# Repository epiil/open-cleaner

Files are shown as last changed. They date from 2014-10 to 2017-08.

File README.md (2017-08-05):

# opencleaner: open-source videotape cleaning

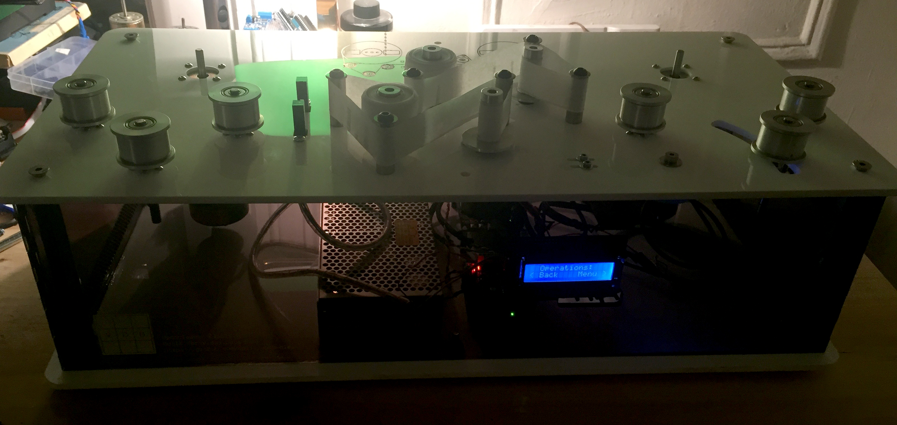
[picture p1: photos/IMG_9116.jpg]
Opencleaner


## Introduction

This repo contains instructions for assembling, testing, and operating an open-reel 1/2" magnetic videotape cleaner. When used in conjunction with other remediation treatments like incubation, tape cleaning assists in minimizing the effects of tape degradation such as binder hydrolysis ("sticky shed syndrome") during the playback/reformatting process.  

Controlled by an Arduino Uno microcontroller and integrated motor shield, the machine consists of a dual-motor spindle system that moves tape through two Pellon cleaning stations. Tape speed and tension are monitored through feedback from optical encoders attached to each motor's shaft. Each Pellon cleaning station incrementally advances fabric past several contact points.  

In-progress videos:

[02/15/2017 - 24VDC Motor Test](https://vimeo.com/204296759)

[02/23/2017 - PID Control Test](https://vimeo.com/205490774)

##Repository Contents:

- /hardware - contains .dwg, .pdf, .stp and .stl files for enclosure and spindle fabrication.

- /software - contains .ino Arduino sketches (http://www.arduino.cc/).

- /schematics - contains .sch and .pdf schematic files for individual components.

- /photos - photo gallery

## Acknowledgements

This project could not have been possible without the generous contributions from the following people and organizations:

Tim Woolaver

Mike Maxwell

Maurice Schechter

Video Data Bank - Tom Colley, Kristin McDonough

Smithsonian NMAAHC - Walter Forsberg

Signal Culture - Deborah Bernagozzi, Jason Bernagozzi, Hank Rudolph

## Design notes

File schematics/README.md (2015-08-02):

- /ComponentSchematics - contains fact sheets for inividual components

- /png - contains .png image of associated schematic

- /sch - contains .sch schematic files done in Eagle (http://www.cadsoftusa.com/)

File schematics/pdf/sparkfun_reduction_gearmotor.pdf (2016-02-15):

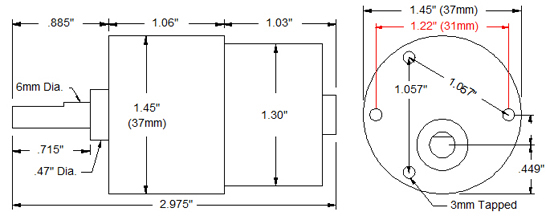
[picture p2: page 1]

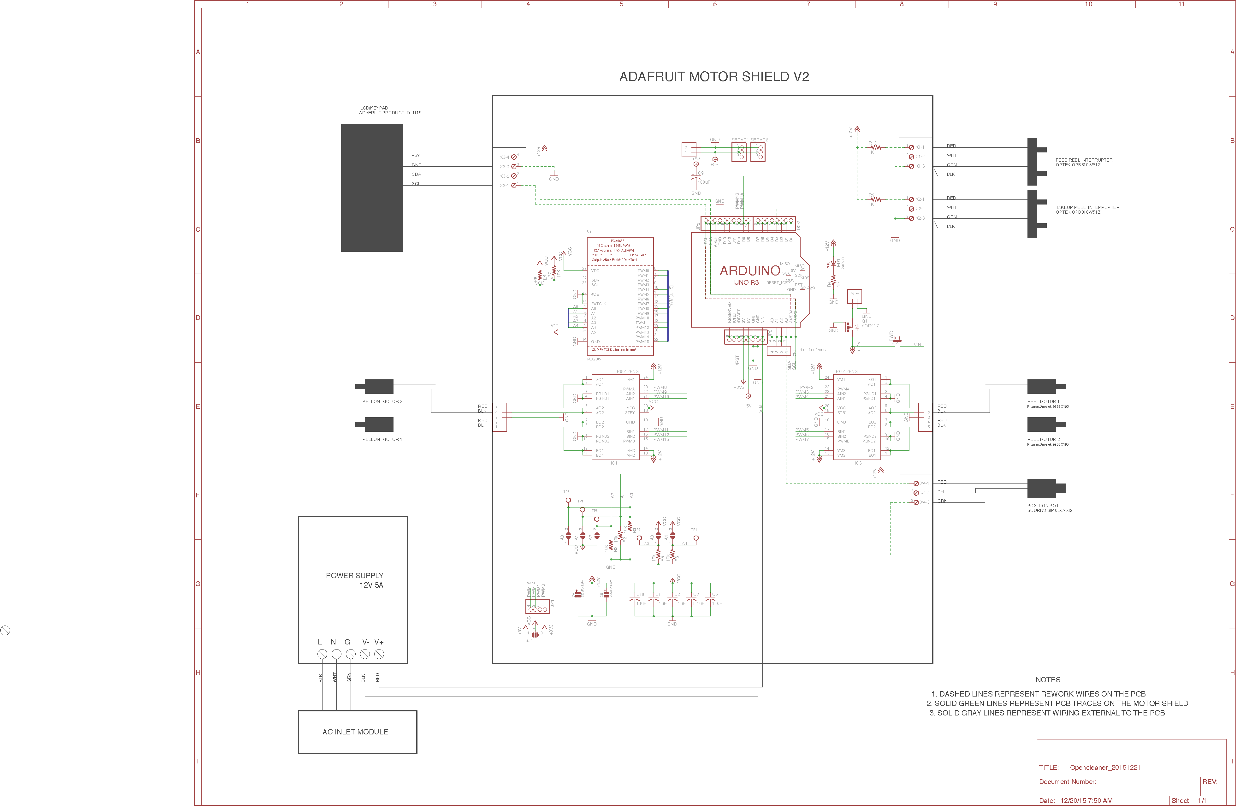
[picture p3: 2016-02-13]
schematics/png/Opencleaner_20151221.png

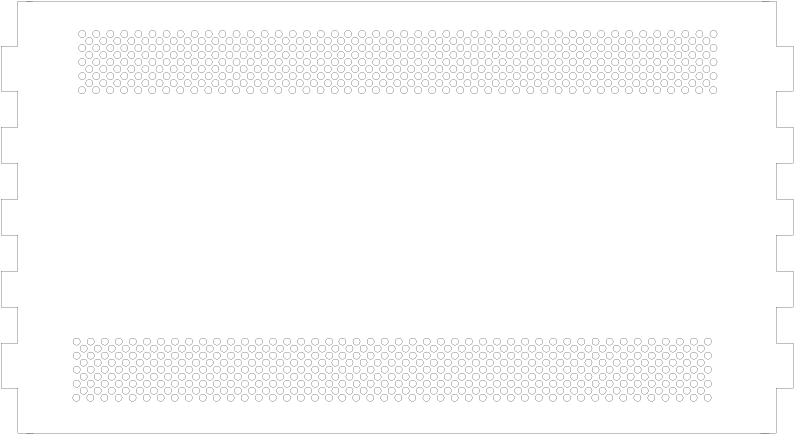
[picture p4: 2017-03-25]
hardware/enclosure/png/20170324 - Opencleaner - Side Panels.png

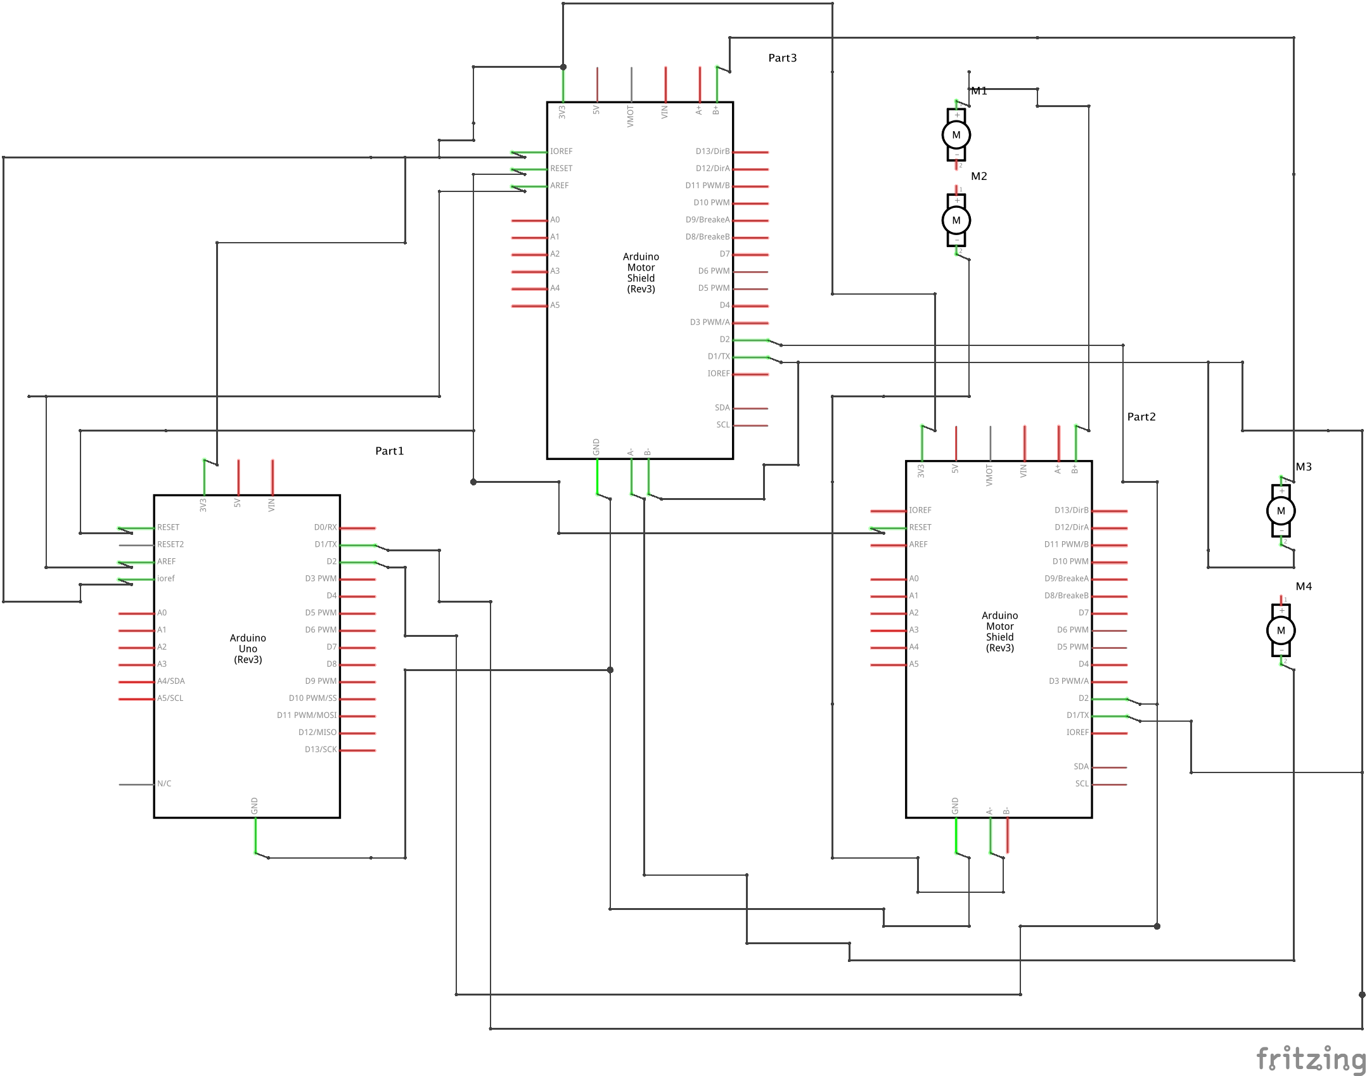
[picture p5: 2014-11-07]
hardware/3_circuit_schematics/png/20141106_tape_cleaner_schem.png

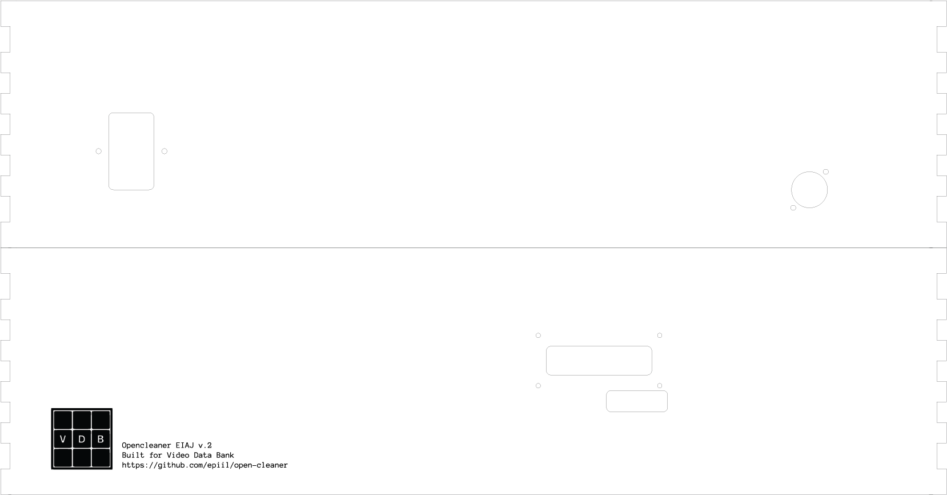
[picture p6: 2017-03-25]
hardware/enclosure/png/20160324 - OpenCleaner - FrontBack Panel.png

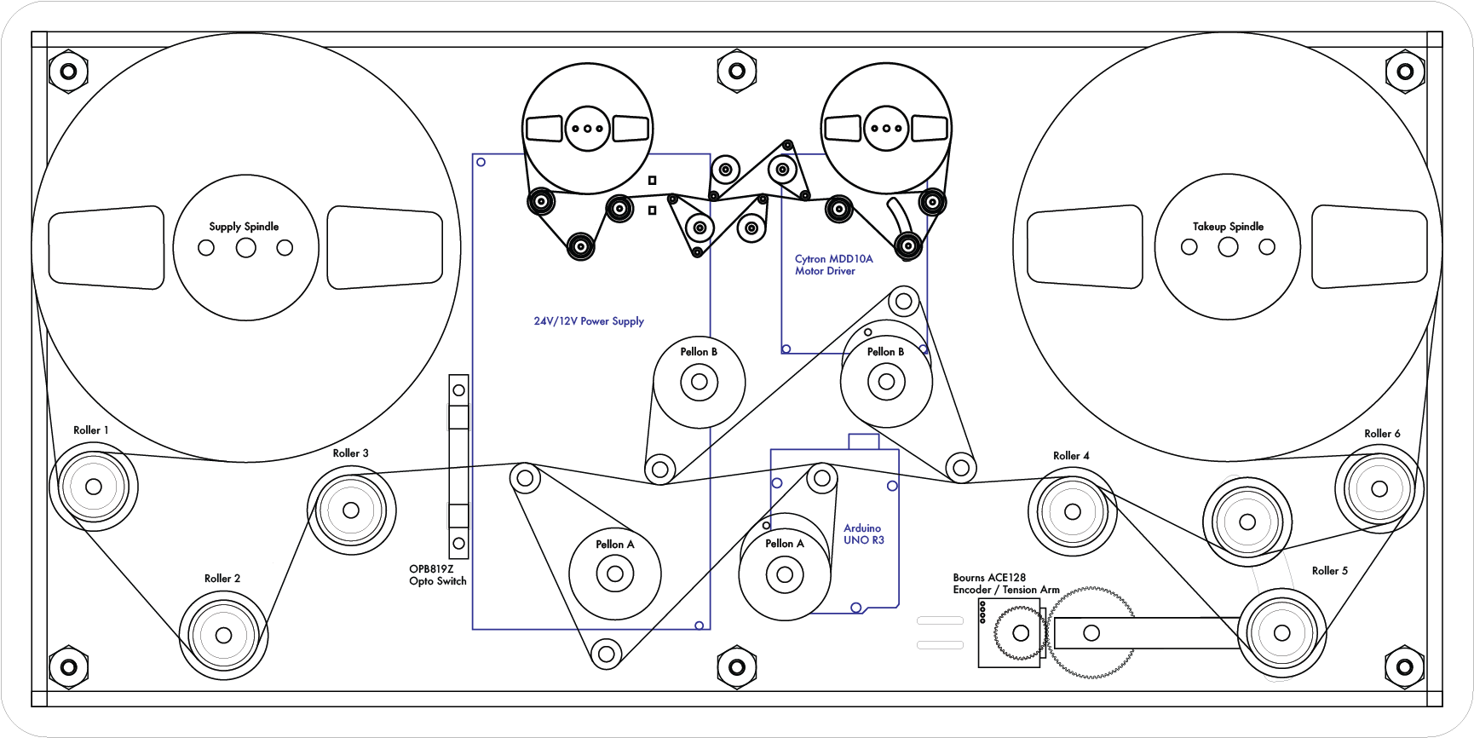
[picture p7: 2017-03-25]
hardware/enclosure/png/20170323 - Opencleaner - Top Panel.png

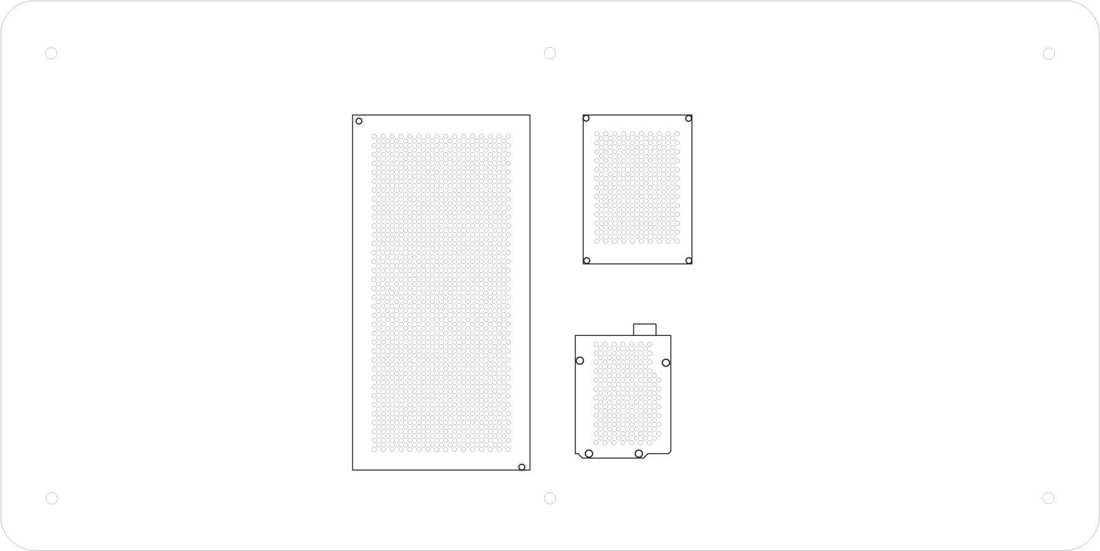
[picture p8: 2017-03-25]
hardware/enclosure/png/20170323 - Opencleaner - Bottom Panel.png

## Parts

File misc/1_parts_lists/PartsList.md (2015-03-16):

##Parts List (Updated 11/18/2014)

###Enclosure

- (1) 350DT 16"W x 16"D aluminum desktop enclosure, natural finish
- Chassis: Extruded Aluminum (6063 T6)
- Top/Bottom/Endplates: Aluminum (5052 H32)

###Main circuit boards / microcontrollers

- (1) Arduino Uno Rev3 Microcontroller board
- (1) Arduino Motor Shield Rev3 (http://arduino.cc/en/Main/ArduinoMotorShieldR3)
- (2) Sparkfun Photo Interrupter Breakout Board - GP1A57HRJ00F

###Motors

- (2) Seiko Continuous Sweep Hi-Torque Quartz Clock Motors
- (2) Brushed DC Motors 

###Cleaning fabric

- (2) Amber Professional Pellon Non-Woven Rolls

###Circuit components

- (2) TIP120 Power Darlington Transistors
- (2) NPN Bipolar Transistors (PN2222) 
- (2) 1N4001 Diodes
- (2) 330 Ohm resistors
- (2) Photo Interrupters - GP1A57HRJ00F
- (1) DPDT switch
- (1) SPDT switch
- (2) LM317TG voltage regulators
- (2) Heatsinks TO-220
- (2) 0.1uF capacitors
- (2) Sharp GP2Y0A21YK0F IR Range Sensors
- (2) SIRC-01 Sharp GP2 IR Sensor Cables

###Misc.

- (1) IEC 320 C14 Male Plug 3 Pins PCB Panel Power Inlet Socket Connector

-----

###(Updated 11/18/2014)

- $ 24.99 (1) Arduino Uno Rev3 
- $ 24.99 (1) Arduino Motor Shield Rev3
- $ 29.90 (2) Seiko Continuous Sweep Hi-Torque Quartz Clock Motors
- $ 33.94 (2) Amber Professional Pellon Non-Woven Rolls
- $ 40.00 (2) Brushed DC Motors
- $  2.50 (1) TIP120 Power Darlington Transistors - 3 pack[ID:976] via Adafruit
- $  1.95 (1) NPN Bipolar Transistors (PN2222) - 10 pack[ID:756] via Adafruit
- $  3.00 (2) 1N4001 Diode - 10 pack[ID:755] via Adafruit
- $  3.00 (2) Sparkfun Photo Interrupter Breakout Board - GP1A57HRJ00F
- $   .50 (2) 330 Ohm resistors
- $  3.90 (2) Photo Interrupters - GP1A57HRJ00F
- $  1.95 (1) DPDT switch
- $  1.95 (1) SPDT switch
- $  7.80 (2) LM317TG voltage regulators
- $  3.80 (2) Heatsinks TO-220
- $   .50 (2) 0.1uF capacitors
- $ 19.90 (2) Sharp GP2Y0A21YK0F IR Range Sensors
- $  3.90 (2) SIRC-01 Sharp GP2 IR Sensor Cables
- $142.95 (1) 350DT 16"W x 16"D aluminum desktop enclosure, natural finish

- $351.42 Total

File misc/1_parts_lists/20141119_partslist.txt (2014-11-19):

Parts List (Updated 11/18/2014)

1. Main circuit boards / microcontrollers

(1) Arduino Uno Rev3 Microcontroller board
(1) Arduino Motor Shield Rev3 (http://arduino.cc/en/Main/ArduinoMotorShieldR3)
(2) Sparkfun Photo Interrupter Breakout Board - GP1A57HRJ00F

2. Motors

(2) Seiko Continuous Sweep Hi-Torque Quartz Clock Motors
(2) Brushed DC Motors 

3. Cleaning fabric

(2) Amber Professional Pellon Non-Woven Rolls

4. Circuit components

(2) TIP120 Power Darlington Transistors
(2) NPN Bipolar Transistors (PN2222) 
(2) 1N4001 Diodes
(2) 330 Ohm resistors
(2) Photo Interrupters - GP1A57HRJ00F
(1) DPDT switch
(1) SPDT switch
(2) LM317TG voltage regulators
(2) Heatsinks TO-220
(2) 0.1uF capacitors

-----

Price List (Updated 11/18/2014)

$24.99 (1) Arduino Uno Rev3 
$24.99 (1) Arduino Motor Shield Rev3
$29.90 (2) Seiko Continuous Sweep Hi-Torque Quartz Clock Motors
$33.94 (2) Amber Professional Pellon Non-Woven Rolls
$40.00 (2) Brushed DC Motors
$ 2.50 (1) TIP120 Power Darlington Transistors - 3 pack[ID:976] via Adafruit
$ 1.95 (1) NPN Bipolar Transistors (PN2222) - 10 pack[ID:756] via Adafruit
$ 3.00 (2) 1N4001 Diode - 10 pack[ID:755] via Adafruit
$ 3.00 (2) Sparkfun Photo Interrupter Breakout Board - GP1A57HRJ00F
$  .50 (2) 330 Ohm resistors
$ 3.90 (2) Photo Interrupters - GP1A57HRJ00F
$ 1.95 (1) DPDT switch
$ 1.95 (1) SPDT switch
$ 7.80 (2) LM317TG voltage regulators
$ 3.80 (2) Heatsinks TO-220
$  .50 (2) 0.1uF capacitors

$184.67 Total

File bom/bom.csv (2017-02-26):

Component | Quantity | Item | Vendor | Price Per Item | Line Total | Item link
Rollers | 6 | Precision Rollers | tnsmachineworks.com | $55.00 | $330.00 | N/A
Cleaning Station | 4 | Pellon Mounts | tnsmachineworks.com | $40.00 | $160.00 | N/A
Reel Spindles | 2 | Spindle Mounts | tnsmachineworks.com | $40.00 | $80.00 | N/A
Electronics | 1 | Arduino Uno Rev3 Microcontroller board | adafruit.com | $24.95 | $24.95 | https://www.adafruit.com/products/50
Electronics | 1 | Adafruit Motor/Stepper/Servo Shield for Arduino v2 Kit (v2.3) | adafruit.com | $19.95 | $19.95 | https://www.adafruit.com/products/1438
Electronics | 1 | Adafruit Blue&White 16x2 LCD+Keypad Kit | adafruit.com | $19.95 | $19.95 | https://www.adafruit.com/products/1115
Electronics | 1 | Cytron MDD10A DC Motor Driver | robotshop.com | $23.49 | $23.49 | http://www.robotshop.com/en/10a-5-30v-dual-channel-dc-motor-driver.html
Electronics | 4 | Brass M2.5 Standoffs for Pi HATs - Black Plated - Pack of 2[ID:2336] | adafruit.com | $3.00 | $12.00 | https://www.adafruit.com/products/2336
Electronics | 1 | 2.54mm/0.1" Pitch Terminal Block - 4-pin[ID:2137] | adafruit.com | $1.55 | $1.55 | https://www.adafruit.com/products/2137
Electronics | 3 | 2.54mm/0.1" Pitch Terminal Block - 3-pin[ID:2136] | adafruit.com | $3.75 | $11.25 | https://www.adafruit.com/product/2
Electronics | 1 | Hook-up Wire Spool Set - 22AWG Solid Core - 6 x 25 ft | adafruit.com | $15.95 | $15.95 | https://www.adafruit.com/products/1311
Electronics | 2 | USB Cable - Standard A-B - 3 ft/1m | adafruit.com | $3.95 | $7.90 | https://www.adafruit.com/products/62
Motors | 2 | 24V/30.3V DC Motors with optical encoders | ebay.com | $50.00 | $100.00 | N/A
Electronics | 1 | Green LED Rocker Switch Fuse Holder IEC320 C14 Inlet Power Socket AC250V 10A | ebay.com | $1.72 | $1.72 | http://www.ebay.com/itm/1x-Green-LED-Rocker-Switch-Fuse-Holder-IEC320-C14-Inlet-Power-Socket-AC250V-10A-/291186777350
Electronics | 1 | AC 110-220V TO DC 12V/24V Regulated Transformer Power Supply | ebay.com | $20.00 | $20.00 | N/A
Electronics | 1 | Zinc Plated Steel Hex Nut, Class 8, M2x0.4 Thread Size, 4mm Wide, 1.6mm High, 100 pack | mcmaster.com | $2.08 | $2.08 | http://www.mcmaster.com/#steel-hex-nuts/=114isxv
Electronics | 1 | Type 316 Stainless Steel Flat Washer, M2 Screw Size, 2.2mm ID, 5.0mm OD | mcmaster.com | $2.37 | $2.37 | http://www.mcmaster.com/#standard-flat-washers/=114iudk
Cleaning Station | 1 | Nylon Unthreaded Spacer, 5/8" OD, 1-1/2" Length, 1/4" Screw Size 10 pack | mcmaster.com | $8.10 | $8.10 | http://www.mcmaster.com/#nylon-spacers/=114j793
Electronics | 1 | Black-Oxide Class 12.9 Socket Head Cap Screw, Alloy Steel, M2 Thread, 20 mm Long, 0.4 mm Pitch 100 Pack | mcmaster.com | $11.16 | $11.16 | http://www.mcmaster.com/#socket-head-cap-screws/=114j98y
Cleaning Station | 1 | 18-8 Stainless Steel Pan Head Phillips Machine Screw, 1/4"-20 Thread, 2-1/2" Length | mcmaster.com | $13.21 | $13.21 | http://www.mcmaster.com/#machine-screws/=114jb3h
Cleaning Station | 1 | Cadmium Chromate Plated Steel Mil. Spec. Hex Nut, Grade 5, 5/8"-11 Thread Size, 15/16" Wide, MS-51967-20 | mcmaster.com | $7.17 | $7.17 | http://www.mcmaster.com/#ms-51967-20-hex-nuts/=114jbhf
Enclosure | 2 | Optically Clear Cast Acrylic Sheet, 1/4" Thick, 12" x 24" | mcmaster.com | $28.08 | $56.16 | http://www.mcmaster.com/#catalog/122/3624/=114hp2r
Enclosure | 3 | Optically Clear Cast Acrylic Rectangular Bar, 1/4" Thick, 4" Width, Clear | mcmaster.com | $3.67 | $11.01 | http://www.mcmaster.com/#catalog/122/3625/=114hpku
Enclosure | 6 | Electrical-Insulating Female Threaded Standoff, Glazed Grade L5 Ceramic, 3/4" OD, 4" Length | mcmaster.com | $10.04 | $60.24 | http://www.mcmaster.com/#catalog/122/3292/=114hq6f
Enclosure | 2 | Leveling Mount, Cushion Rest, 1/4"-20 x 7/8" Thread Length, 1-1/4" Base | mcmaster.com | $5.22 | $10.44 | http://www.mcmaster.com/#catalog/122/1416/=114hqkz
Enclosure | 6 | Mil. Spec. Flat-Head Socket Cap Screw, 300 Series Stainless Steel, 1/4"-20 Thread, 3/4" Long, MS24671 | mcmaster.com | $4.75 | $28.50 | http://www.mcmaster.com/#catalog/122/3127/=114hqy4
Cleaning Station | 4 | Idler Shaft, 1/2" OD, 1-1/16" Overall Length, Thread Mount | mcmaster.com | $7.53 | $30.12 | http://www.mcmaster.com/#catalog/122/1123/=114ht8p
Tension Arm | 1 | Precision Stainless Steel Extension Spring, 1.0" Length, .250" OD, .026" Wire Diameter | mcmaster.com | $4.29 | $4.29 | http://www.mcmaster.com/#catalog/122/1265/=114htt8
Tension Arm | 1 | Steel Extension Spring Anchor Stud, Standard, 1/4"-20 Thread, 1-1/4" Overall Length | mcmaster.com | $3.22 | $3.22 | http://www.mcmaster.com/#catalog/122/1264/=114hua6
Rollers | 1 | 18-8 Stainless Steel Button-Head Socket Cap Screw, 4-40 Thread, 1" Length | mcmaster.com | $4.54 | $4.54 | http://www.mcmaster.com/#catalog/122/3128/=114hutl
Rollers | 6 | Black-Finish Aluminum Unthreaded Spacer, 1/2" OD, 1/4" Length, #1/4 Screw Size | mcmaster.com | $2.69 | $16.14 | http://www.mcmaster.com/#catalog/122/3283/=114hva5
Cleaning Station | 1 | Low-Strength Steel Extra-Wide Thin Hex Nut, Black Oxide, 1/4"-20 Thread Size, 1/2" Wide, 11/64" High | mcmaster.com | $6.05 | $6.05 | http://www.mcmaster.com/#catalog/122/3209/=114hwkl
Cleaning Station | 1 | Black-Oxide 18-8 Stainless Steel Flat Washer, Oversized, 1/4" Screw Size, 0.266" ID, 1.500" OD | mcmaster.com | $7.30 | $7.30 | http://www.mcmaster.com/#catalog/122/3239/=114hx86
Rollers | 8 | 303 Stainless Steel Shaft with Retaining Ring Grooves, 1/4" OD, 3" Overall Length | mcmaster.com | $4.52 | $36.16 | http://www.mcmaster.com/#catalog/122/3298/=114hz0p
Rollers | 1 | Stainless Steel External Retaining Ring, for 1/4" Shaft Diameter, packs of 10 | mcmaster.com | $8.50 | $8.50 | http://www.mcmaster.com/#catalog/122/3298/=114hzwu
Rollers | 8 | Steel Ball Bearing--ABEC-1, Double Shielded, No. R4A for 1/4" Shaft Diameter, 3/4" OD | mcmaster.com | $6.90 | $55.20 | http://www.mcmaster.com/#catalog/122/1187/=114hypo
Rollers | 1 | Type 316 Stainless Steel Button-Head Socket Cap Screw, 4-40 Thread, 1/2" Length, packs of 50 | mcmaster.com | $2.98 | $2.98 | http://www.mcmaster.com/#catalog/122/1122/=114hy3p
Cleaning Station | 2 | Standard Gearmotor - 1 RPM (3-12V) | sparkfun.com | $24.95 | $49.90 | https://www.sparkfun.com/products/12219
Rollers | 1 | Pololu Universal Aluminum Mounting Hub for 1/4″ Shaft, #4-40 Holes (2-Pack) | pololu.com | $7.95 | $7.95 | https://www.pololu.com/product/1993
Tension Arm | 1 | Bourns Inc. EM14A0D-C24-L064N ENCODER OPT ROTARY 64PPR WO/SW | digikey.com | $29.18 | $29.18 | http://www.digikey.com/product-detail/en/EM14A0D-C24-L064N/EM14A0D-C24-L064N-ND/2537991
Electronics | 1 | Switchcraft EHUSBBAX USB-B to USB-A Panel Mount Connector | markertek.com | $6.24 | $6.24 | http://www.markertek.com/product/ehusbba/switchcraft-ehusbbax-usb-b-to-usb-a-panel-mount-connector-silver

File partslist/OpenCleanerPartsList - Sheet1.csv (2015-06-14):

Quantity | Item | Vendor | Price Per Item | Line Total | Item link
1 | 350DT 16"W x 16"D aluminum desktop enclosure, natural finish; Extruded Aluminum (6063 T6); - Top/Bottom/Endplates: Aluminum (5052 H32) | EnclosuresAndCases.com | $202.95 | $202.95 | N/A
1 | Arduino Uno Rev3 Microcontroller board OR (1) Arduino Mega 2560 Microcontroller Board | Adafruit.com | $45.95 | $45.95
1 | Adafruit Motor/Stepper/Servo Shield for Arduino v2 Kit (v2.3) | Adafruit.com | $19.95 | $19.95
2 | DC 6V 30RPM Micro Speed Reduction Gear Motor with Metal Gearbox Wheel 3mm Shaft | Newegg.com | $7.34 | $14.68 | http://www.newegg.com/Product/Product.aspx?Item=9SIA76H2TP7945
2 | Sharp GP2Y0A21YK0F IR Range Sensors | Digikey.com | $7.50 | $15.00 | http://www.digikey.com/product-detail/en/GP2Y0A41SK0F/425-2819-ND/3884447
2 | SIRC-01 Sharp GP2 IR Sensor Cables | Digikey.com | $2.00 | $4.00
4 | M3-0.5 x 16mm Metric Socket Cap Screws | HomeDepot.com | $1.00 | $4.00
4 | M3-0.5 X 16mm Steel Hex Nuts | HomeDepot.com | $1.00 | $4.00
2 | IR distance sensor mounts (For 3D printing: https://github.com/epiil/open-cleaner/blob/master/hardware/3_ir_distance_sensor_holder/stl/ir_distance_sensor_holder.stl) | N/A | $5.00 | $10.00 | N/A
2 | OPTEK SENS OPTO SLOT 9.53MM TRANS C-MT Photointerrupters | Digikey.com | $3.82 | $7.64
1 | Bourns Inc. 3046L-3-502 Linear Position Potentiometer | Digikey.com | $14.35 | $14.35
1 | Adafruit Blue&White 16x2 LCD+Keypad Kit | Adafruit.com | $19.95 | $19.95 | https://www.adafruit.com/products/1115
4 | M2-0.4 x 20mm Metric Socket Cap Screws | HomeDepot.com | $1.00 | $4.00
4 | M2-0.4 Steel Hex Nuts | HomeDepot.com | $1.00 | $4.00
8 | M2-0.4 Flat Washers | HomeDepot.com | $0.50 | $4.00
2 | Amber Professional Pellon Non-Woven Rolls | http://www.theindustrysource.com/ | $16.99 | $33.98
6 | 1/4"-20 x2" stainless phillips machine screws | HomeDepot.com | $0.50 | $3.00
2 | 1/2" O.D. .257" I.D. 1" length nylon bushings | HomeDepot.com | $1.00 | $2.00
6 | 3/8" x 1/2" x 1-1/2" metal bushings | HomeDepot.com | $1.00 | $6.00
2 | TE Connectivity AMP Connectors 282834-3 Terminal Blocks | Digikey.com | $1.51 | $3.02
1 | SODIAL IEC 320 C14 Male Plug 3 Pins PCB Panel Power Inlet Socket Connector | Digikey.com | $2.00 | $2.00 | http://www.digikey.com/scripts/DkSearch/dksus.dll?Detail&itemSeq=174117518&uq=635698108684045928
1 | SPST On/Off Rocker Switch | Amazon.com | $2.00 | $2.00
1 | Switchcraft EHUSBBABX USB-B to USB-A Panel Mount Feed Through USB Barrel Connector | Markertek.com | $5.99 | $5.99
1 | USB cable, 1.5 feet (A male to B male) | Markertek.com | $5.89 | $5.89 | http://www.markertek.com/product/trl-ur022-003/tripp-lite-ur022-003-usb-2-0-reversible-a-male-to-b-male-cable-3-ft
1 | USB cable, 3 feet (A male to B male) | Markertek.com | $5.89 | $5.89 | http://www.markertek.com/product/trl-ur022-003/tripp-lite-ur022-003-usb-2-0-reversible-a-male-to-b-male-cable-3-ft
 |  |  | Parts Total | $444.24

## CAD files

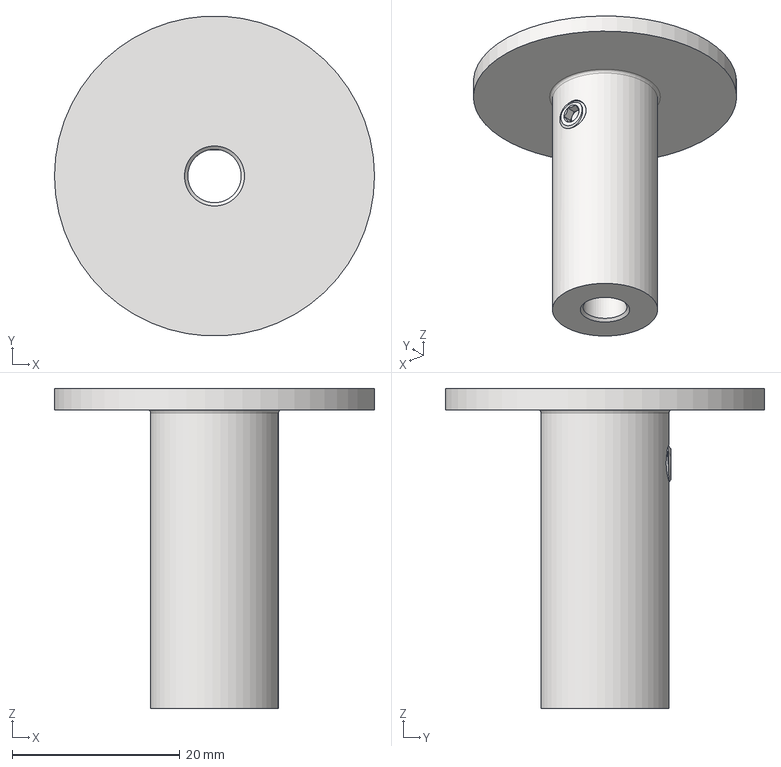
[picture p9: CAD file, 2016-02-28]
hardware/pellon_mounts/stp/Pellon Mount Assembly.stp
38.1 x 38.0 x 38.1 mm

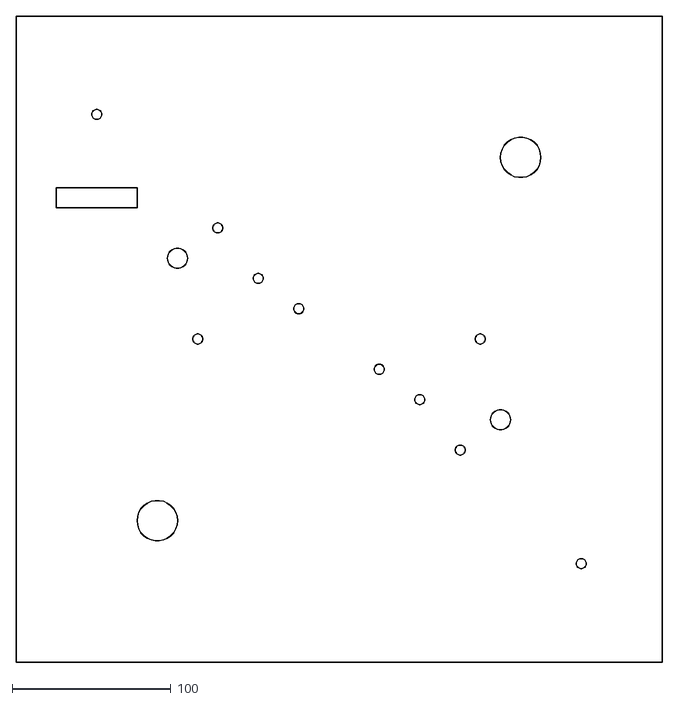
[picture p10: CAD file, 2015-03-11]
hardware/1_tape_cleaner_enclosure/dxf/Enclosuretop2D.dxf
406.4 x 406.4

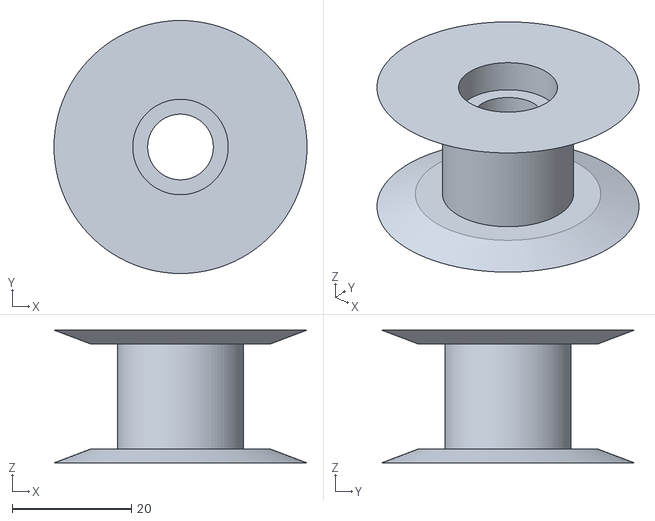
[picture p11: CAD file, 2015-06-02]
hardware/4_tape_cleaner_roller/stl/tape_path_roller.stl
42.4 x 42.4 x 22.3

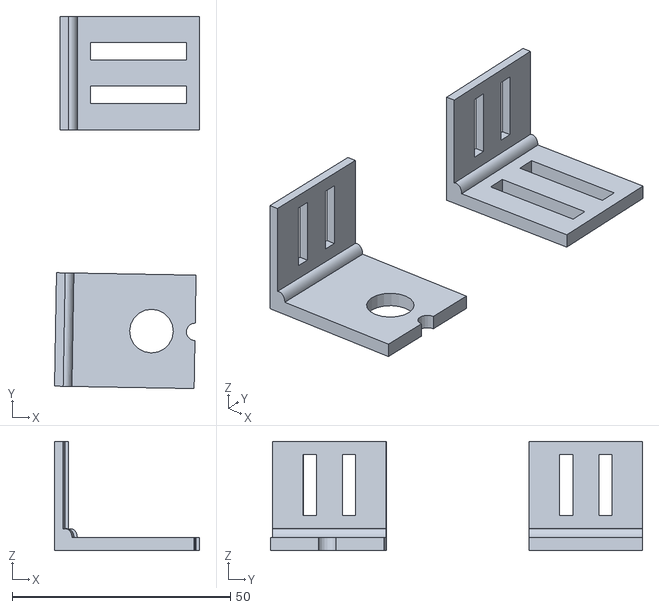
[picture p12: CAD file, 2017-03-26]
hardware/ACE128 mounts/UM2_ACEmounts.stl
33.2 x 85.3 x 25.0

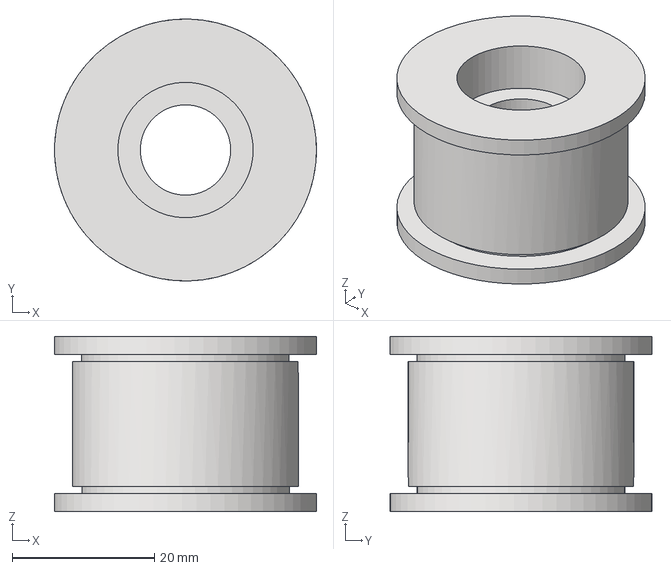
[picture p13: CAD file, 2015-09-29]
hardware/pecision_rollers/stp/precision_roller.stp
36.8 x 36.8 x 24.6 mm

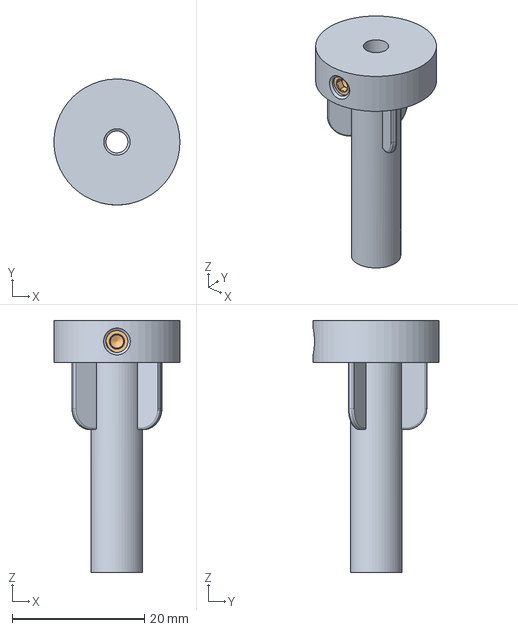
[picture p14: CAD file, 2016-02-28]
hardware/spindles/stp/1212094 - Spindle Assembly.stp
19.0 x 19.0 x 38.1 mm

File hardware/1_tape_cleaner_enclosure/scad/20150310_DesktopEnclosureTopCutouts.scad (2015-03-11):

// tape cleaner enclosure top
// Erik Piil
//piil.erik@gmail.com
//https://github.com/epiil/tape-cleaner
//v20150310

//OUTER DIMENSIONS in mm

outerWidth=406.4;
outerLength=406.4;
outerHeight=2.286;


module top()
{
	difference() 
	{
		union() 
		{
			cube(size=[outerWidth, outerLength, outerHeight], center = true, $fs=.01);
		}
		union() 
		{
			translate([114.3,114.3,0])
			cylinder(h=5, d=25.4, center = true, $fs=.01);
             translate([-114.3,-114.3,0])
			cylinder(h=5, d=25.4, center = true, $fs=.01);
             translate([-152.4,141.2875,0])
			cylinder(h=5, d=6.35, center = true, $fs=.01);
             translate([152.4,-141.2875,0])
			cylinder(h=5, d=6.35, center = true, $fs=.01);
             translate([-76.2,69.85,0])
			cylinder(h=5, d=6.35, center = true, $fs=.01);
             translate([76.2,-69.85,0])
			cylinder(h=5, d=6.35, center = true, $fs=.01);
             translate([-25.4,19.05,0])
			cylinder(h=5, d=6.35, center = true, $fs=.01);
             translate([25.4,-19.05,0])
			cylinder(h=5, d=6.35, center = true, $fs=.01);
             translate([-88.9,0,0])
			cylinder(h=5, d=6.35, center = true, $fs=.01);
             translate([88.9,0,0])
			cylinder(h=5, d=6.35, center = true, $fs=.01);
             translate([-50.8,38.1,0])
			cylinder(h=5, d=6.35, center = true, $fs=.01);
             translate([50.8,-38.1,0])
			cylinder(h=5, d=6.35, center = true, $fs=.01);
             translate([-101.6,50.8,0])
			cylinder(h=5, d=12.7, center = true, $fs=.01);
             translate([101.6,-50.8,0])
			cylinder(h=5, d=12.7, center = true, $fs=.01);
		}
	}
}

top();

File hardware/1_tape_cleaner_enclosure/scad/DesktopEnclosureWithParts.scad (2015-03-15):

// tape cleaner enclosure top
// Erik Piil
//piil.erik@gmail.com
//https://github.com/epiil/tape-cleaner
//v20150310

//OUTER DIMENSIONS in mm

outerWidth=406.4;
outerLength=406.4;
outerHeight=2.286;

//SPINDLE "OUTER" PARAMETERS
outerRadius=60; //outer "seat" radius
outerDiam=120; //outer "seat" diameter
outerHeight=2; //outer "seat" height


//SPINDLE "INNER" DIAMETERS
innerRadius=13.5; //inner spindle radius
innerDiam=29.62; //inner spindle diameter
innerHeight=20; //inner spindle height
shaftDiam=8; //inner shaft diameter
shaftRadius=4; //inner shaft radius

//TEETH PARAMETERS

prongNum=3; //number of prongs (int)
prongRadius=1.92;
prongDiam=3.84;
prongHeight=3.93;
shaftteethNum = 3; //number of teeth 
addendum = 3/2;
dedendum = 3/2;
shafttoothWidth = 3/2;

include<arduino.scad>


module top()
{
	difference() 
	{
		union() 
		{
			color([.5,.5,.5,1])
			cube(size=[outerWidth, outerLength, outerHeight], center = true, $fs=.01);
		}
		union() 
		{
			color([.5,.5,.5,.6])
			translate([114.3,114.3,0])
			cylinder(h=5, d=58, center = true, $fs=.01); //supply motor spindle cutout
             	translate([-114.3,-114.3,0])
			cylinder(h=5, d=58, center = true, $fs=.01); //takeup motor supply cutout
             	translate([-136,152.4,0]) 
			cylinder(h=5, d=6.35, center = true, $fs=.01); //supply corner roller
             	translate([136,-152.4,0])
			cylinder(h=5, d=6.35, center = true, $fs=.01); // takeup corner roller
             	translate([-69, 77.7,0])  
			cylinder(h=5, d=6.35, center = true, $fs=.01); //cleaning path guide roller A
             	translate([69,-77.7,0])
			cylinder(h=5, d=6.35, center = true, $fs=.01); //cleaning path guide roller B
             	translate([-18.2, 26.9,0])
			cylinder(h=5, d=6.35, center = true, $fs=.01); //cleaning path guide roller C
             	translate([18.2, -26.9,0]) 
			cylinder(h=5, d=6.35, center = true, $fs=.01); //cleaning path guide roller D
             	translate([-7,92,0]) 
			cylinder(h=5, d=6.35, center = true, $fs=.01); //cleaning path guide roller E
             	translate([7,-92,0])
			cylinder(h=5, d=6.35, center = true, $fs=.01); //cleaning path guide roller F
             	translate([-30,65,0])  
			cylinder(h=5, d=6.35, center = true, $fs=.01); //cleaning path guide roller G //supply-side supply pellon
             	translate([30,-65,0])
			cylinder(h=5, d=6.35, center = true, $fs=.01); //cleaning path guide roller H //takeup-side supply pellon
             	translate([-50.8,108,0]) 
			cylinder(h=5, d=12.7, center = true, $fs=.01); //cleaning path guide roller I //supply-side takeup pellon
             	translate([50.8,-108,0])
			cylinder(h=5, d=12.7, center = true, $fs=.01); //cleaning path guide roller J //takeup-side takeup pellon
            	translate([-80.7, 152.4,0]) 
			rotate(90) cube(size=[50.8, 10.5, 5], center = true, $fs=.01); //tension arm roller cutout
           		translate([-25.4, 152.4,0]) 
			cylinder(h=5, d=6.35, center = true, $fs=.01); //supplyside initial roller
	        	translate([-25.4,-25.4,0])
			rotate(45) cube(size=[40, 10.5, 5], center = true, $fs=.01); //IR sensor takeup side
	        	translate([25.4, 25.4,0])
			rotate(45) cube(size=[40, 10.5, 5], center = true, $fs=.01); //IR sensor supply side
	        	translate([-127, 127,0])
			rotate(45) cube(size=[35, 5.1, 5], center = true, $fs=.01); //photoop sensor takeup side
	        	translate([127, -127,0])
			rotate(45) cube(size=[35, 5.1, 5], center = true, $fs=.01); //photoop sensor supply side
		}
	}
}

top();

module spindlesupply() //UMatic spindle for the supply side
{
	difference()
	{
		union()
		color("black")
		{
			translate([-114.3,-114.3,0])
			cylinder(r=outerRadius, h=outerHeight, $fs=.01);
			translate([-114.3,-114.3,0])
			cylinder(d=innerDiam, h=innerHeight, $fs=.01);
			translate([-123.3,-114,0])
			cylinder(h=innerHeight+prongHeight, r=prongRadius);
			translate([-110.3,-122,0])
			cylinder(h=innerHeight+prongHeight, r=prongRadius);
			translate([-109.3,-106,0])
			cylinder(h=innerHeight+prongHeight, r=prongRadius);
			{

			}
		}
		
		union()
		color("black")
		{
			translate([-114.3,-114.3,0])
			cylinder(r=shaftRadius, h=innerHeight*2+1, center=true);
			translate([0,0,10/2]) spur(3, 8, 10);
			if (centerShape==1) solid(10, 8);	
			{
			}
		}
	}
}



spindlesupply(); 

module spindletakeup() //UMatic spindle for the takeup side
{
	difference()
	{
		union()
		color("black")
		{
			translate([114.3,114.3,0])
			cylinder(r=outerRadius, h=outerHeight, $fs=.01);
			translate([114.3,114.3,0])
			cylinder(d=innerDiam, h=innerHeight, $fs=.01);
			translate([123.3,114,0])
			cylinder(h=innerHeight+prongHeight, r=prongRadius);
			translate([110.3,122,0])
			cylinder(h=innerHeight+prongHeight, r=prongRadius);
			translate([109.3,106,0])
			cylinder(h=innerHeight+prongHeight, r=prongRadius);
			{

			}
		}
		
		union()
		color("black")
		{
			translate([114.3,114.3,0])
			cylinder(r=shaftRadius, h=innerHeight*2+1, center=true);
			translate([0,0,10/2]) spur(3, 8, 10);
			if (centerShape==1) solid(10, 8);	
			{
			}
		}
	}
}



spindletakeup();

module guiderollers() //guide rollers 
{
	difference() 
	{
		union() 
		color("silver")
		{
             	translate([-136,152.4,0])
			cylinder(h=38, d=23, $fs=.01); //supply corner roller 
             	translate([136,-152.4,0])
			cylinder(h=38, d=23, $fs=.01); // takeup corner roller
           		translate([-25.4, 152.4,0]) 
			cylinder(h=5, d=6.35, center = true, $fs=.01); //supplyside initial roller
             	translate([-69, 77.7,0])  
			cylinder(h=38, d=12.6, $fs=.01); //cleaning path guide roller A
             	translate([69,-77.7,0])
			cylinder(h=38, d=12.6, $fs=.01); //cleaning path guide roller B
             	translate([-18.2, 26.9,0])
			cylinder(h=38, d=12.6, $fs=.01); //cleaning path guide roller C
             	translate([18.2, -26.9,0])
			cylinder(h=38, d=12.6, $fs=.01); //cleaning path guide roller D
             	translate([-7,92,0])
			cylinder(h=38, d=12.6, $fs=.01); //cleaning path guide roller E
             	translate([7,-92,0])
			cylinder(h=38, d=12.6, $fs=.01); //cleaning path guide roller F
             	translate([-30,65,0])
			cylinder(h=38, d=13.5, $fs=.01); //cleaning path guide roller G //supply-side supply pellon
             	translate([30,-65,0])
			cylinder(h=38, d=13.5, $fs=.01); //cleaning path guide roller H //takeup-side supply pellon
             	translate([-50.8,108,0])
			cylinder(h=38, d=13.5, $fs=.01); //cleaning path guide roller I //supply-side takeup pellon
             	translate([50.8,-108,0])
			cylinder(h=38, d=13.5, $fs=.01); //cleaning path guide roller J //takeup-side takeup pellon
            	translate([-80.7, 152.4,0])
			cylinder(h=38, d=23, $fs=.01); //tension arm roller 
             	translate([-25.4, 152.4,0]) 
			cylinder(h=38, d=23, $fs=.01); //supplyside initial roller
		}
		union()
        color("silver")
		{
             	translate([-136,152.4,0])
			cylinder(h=80, d=6.35, center = true, $fs=.01); //supply corner roller 
             	translate([136,-152.4,0])
			cylinder(h=80, d=6.35, center = true, $fs=.01); // takeup corner roller
             	translate([-69, 77.7,0])
			cylinder(h=80, d=6.35, center = true, $fs=.01); //cleaning path guide roller A
             	translate([69,-77.7,0])
			cylinder(h=80, d=6.35, center = true, $fs=.01); //cleaning path guide roller B
             	translate([-18.2, 26.9,0])
			cylinder(h=80, d=6.35, center = true, $fs=.01); //cleaning path guide roller C
             	translate([18.2, -26.9,0])
			cylinder(h=80, d=6.35, center = true, $fs=.01); //cleaning path guide roller D
             	translate([-7,92,0])
			cylinder(h=80, d=6.35, center = true, $fs=.01); //cleaning path guide roller E
             	translate([7,-92,0])
			cylinder(h=80, d=6.35, center = true, $fs=.01); //cleaning path guide roller F
             	translate([-30,65,0])
			cylinder(h=80, d=6.35, center = true, $fs=.01); //cleaning path guide roller G //supply-side supply pellon
             	translate([30,-65,0])
			cylinder(h=80, d=6.35, center = true, $fs=.01); //cleaning path guide roller H //takeup-side supply pellon
             	translate([-50.8,108,0])
			cylinder(h=80, d=6.35, center = true, $fs=.01); //cleaning path guide roller I //supply-side takeup pellon
             	translate([50.8,-108,0])
			cylinder(h=80, d=6.35, center = true, $fs=.01); //cleaning path guide roller J //takeup-side takeup pellon
            	translate([-80.7, 152.4,0])
			cylinder(h=80, d=6.35, center = true, $fs=.01); //tension arm roller
			translate([-25.4, 152.4,0]) 
			cylinder(h=80, d=6.35, center = true, $fs=.01); //supplyside initial roller
		}
	}
}

guiderollers();
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

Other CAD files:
hardware/pellon_mounts/dwg/Pellon Mount.dwg
hardware/spindles/dwg/1212094 - Spindle.dwg
hardware/2_spindles/scad/20150209_Umatic.scad
hardware/pecision_rollers/dwg/precision_roller.dwg
hardware/pecision_rollers/stl/precision_roller.stl
hardware/pellon_mounts/dwg/Pellon Mount Assembly.dwg
hardware/pellon_mounts/stl/Pellon Mount Assembly.stl
hardware/spindles/dwg/1212094 - Spindle Assembly.dwg
hardware/spindles/stl/1212094 - Spindle Assembly.stl

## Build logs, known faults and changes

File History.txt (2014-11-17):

2014-11-17

-----

+ Added preliminary components for pellon motor system

2014-11-15

-----

+ Added sketch for bidirectional take-up/supply motor testing

2014-11-13

-----

+ Replaced Adafruit Motor Shield with Arduino Motor Shield
+ Added sketch for preliminary DC Motor testing with Arduino Motor Shield
+ Updated parts list - Arduino Motor Shield, Potentiometers, etc. 

2014-11-09

-----

+ Cleaned up file naming conventions, added folder for legacy documents

2014-10-28

-----

+ Revised sketch to include two DC reduction gear motors for pellon cleaning system (removed two servo motors)
+ Moved tape cleaner enclosure design to TinkerCAD
+ Added Arduino sketch for DC motor control with potentiometer (not for use with Adafruit motor shield)

2014-10-22

-----

+ Added preliminary Arduino sketch and motor library, spindle models, etc.

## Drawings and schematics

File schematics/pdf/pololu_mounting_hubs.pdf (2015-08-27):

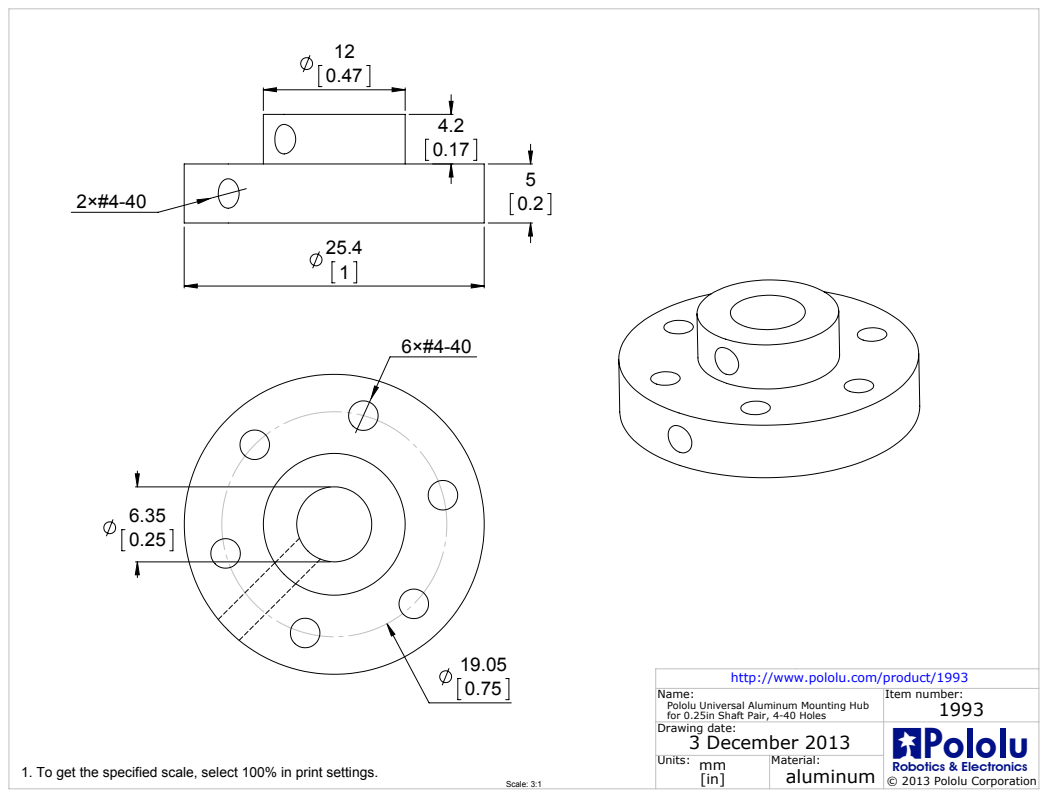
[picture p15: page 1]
Scale: 3:1

Name: Pololu Universal Aluminum Mounting Hub for 0.25in Shaft Pair, 4-40 Holes | Item number: 1993

Drawing date: 3 December 2013 | l l Po o u Robotics & Electronics © 2013 Pololu Corporation

Units: mm [in] | Material: aluminum

1. To get the specified scale, select 100% in print settings.

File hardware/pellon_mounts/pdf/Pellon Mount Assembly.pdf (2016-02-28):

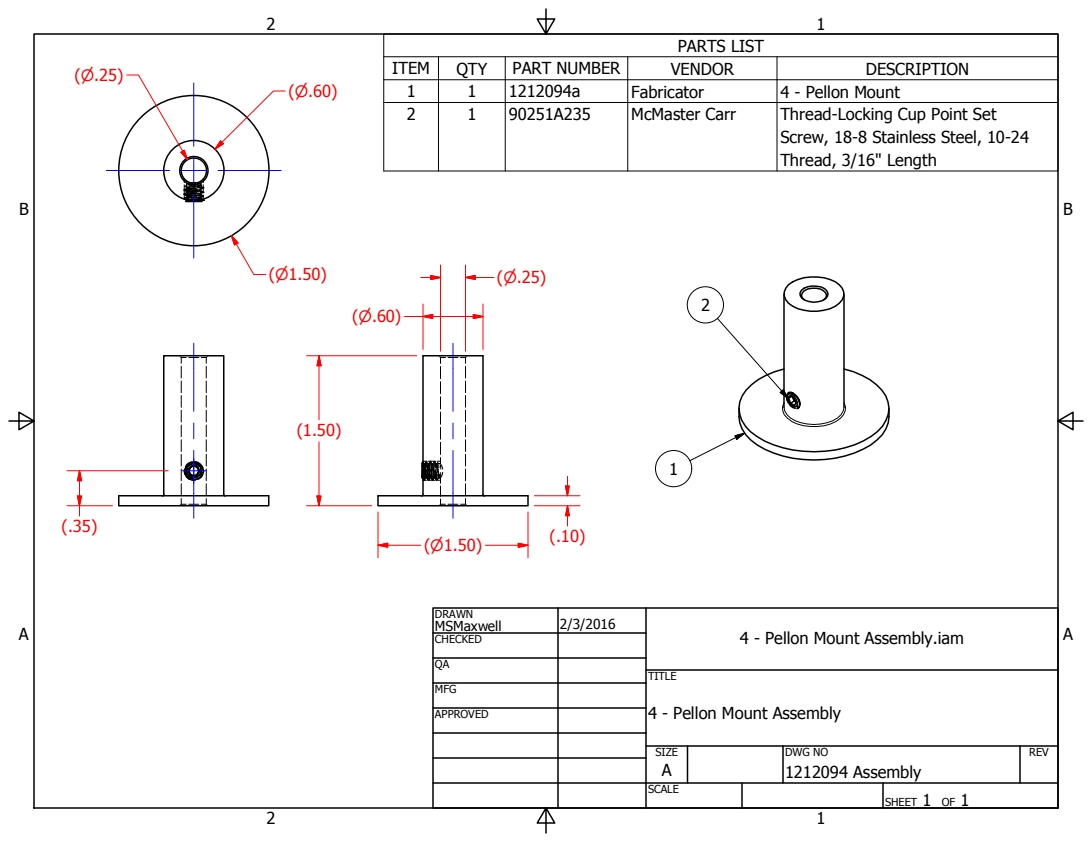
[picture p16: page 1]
PARTS LIST; ITEM; QTY; PART NUMBER; VENDOR; DESCRIPTION; Fabricator; 4 - Pellon Mount; McMaster Carr; DRAWN MSMaxwell CHECKED; MFG; APPROVED; TITLE; SIZE A; SCALE; DWG NO 1212094 Assembly; REV; SHEET 1 OF 1

Thread-Locking Cup Point Set
Screw, 18-8 Stainless Steel, 10-24
Thread, 3/16" Length

4 - Pellon Mount Assembly.iam

4 - Pellon Mount Assembly

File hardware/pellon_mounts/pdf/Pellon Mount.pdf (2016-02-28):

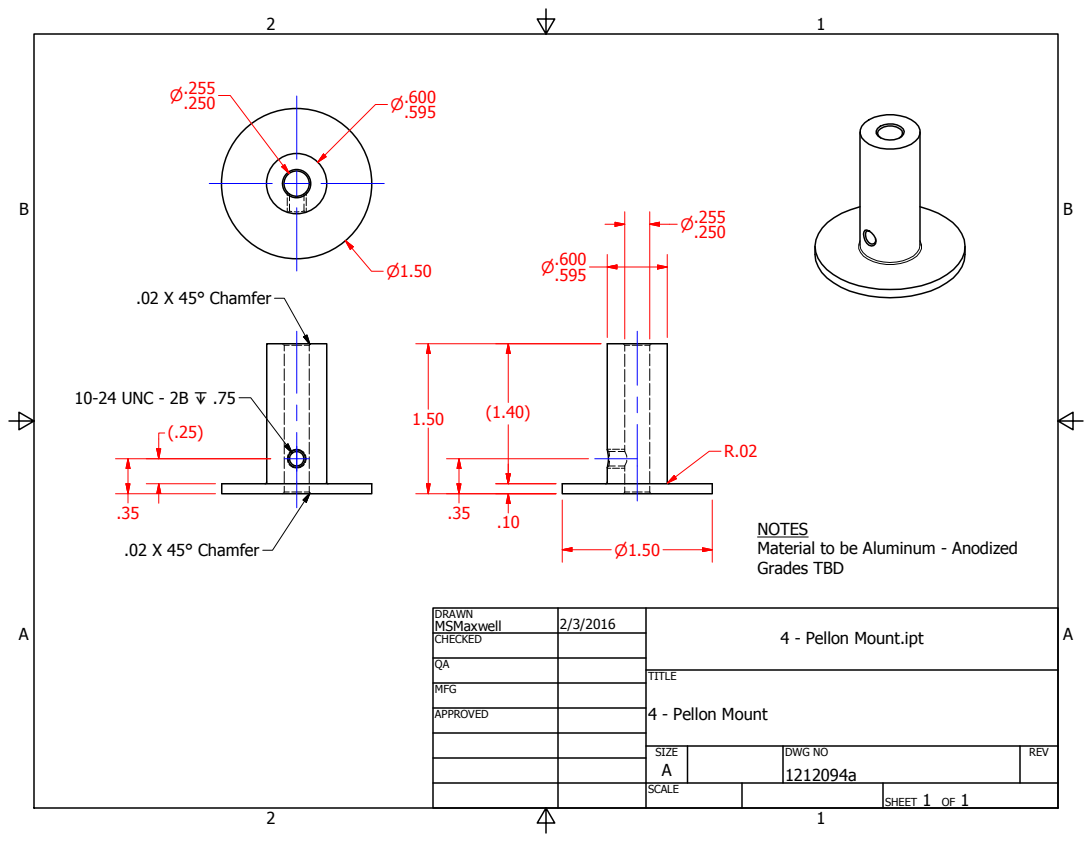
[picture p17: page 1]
DRAWN MSMaxwell CHECKED; MFG; APPROVED; TITLE; 4 - Pellon Mount; SIZE A; SCALE; DWG NO 1212094a; REV; SHEET 1 OF 1; .02 X 45° Chamfer; 10-24 UNC - 2B Z .75

NOTES
Material to be Aluminum - Anodized
Grades TBD

4 - Pellon Mount.ipt

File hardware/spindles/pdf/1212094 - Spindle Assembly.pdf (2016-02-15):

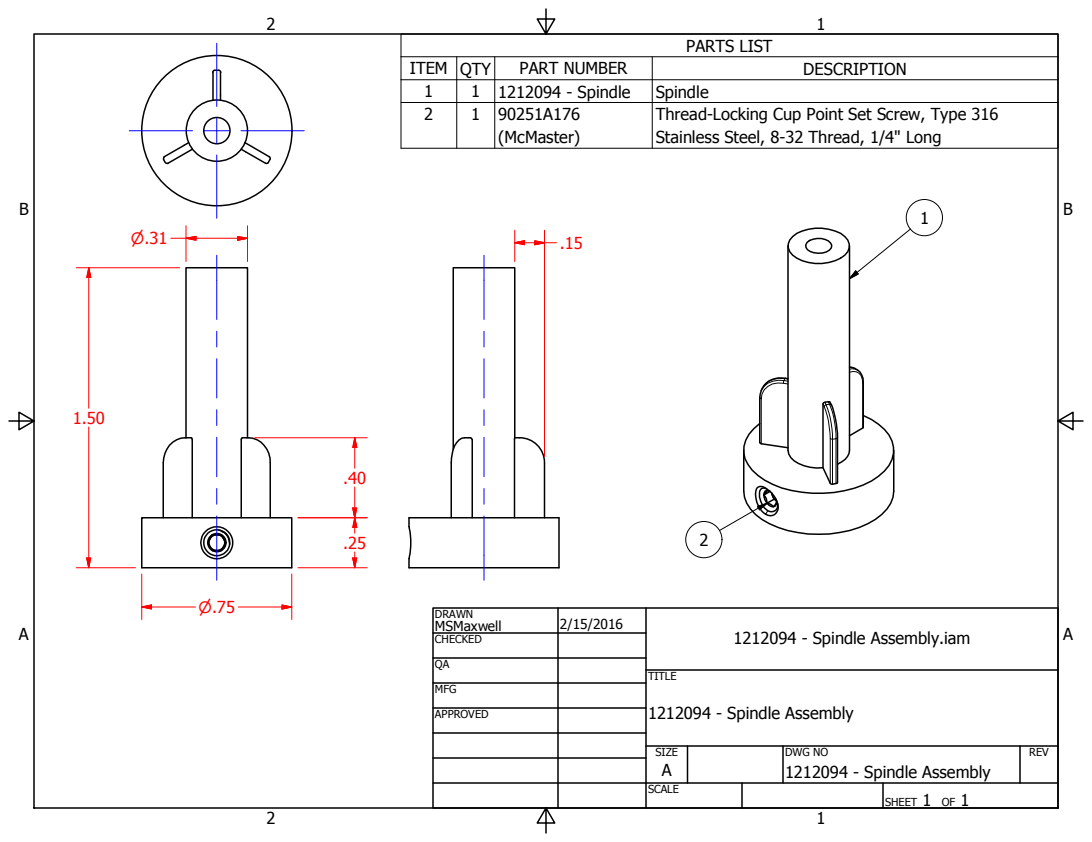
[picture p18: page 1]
PARTS LIST; ITEM; QTY; PART NUMBER; DESCRIPTION; 1212094 - Spindle; Spindle; 90251A176 (McMaster); DRAWN MSMaxwell CHECKED; MFG; APPROVED; TITLE; 1212094 - Spindle Assembly; SIZE A; SCALE; DWG NO 1212094 - Spindle Assembly; REV; SHEET 1 OF 1

Thread-Locking Cup Point Set Screw, Type 316
Stainless Steel, 8-32 Thread, 1/4" Long

1212094 - Spindle Assembly.iam

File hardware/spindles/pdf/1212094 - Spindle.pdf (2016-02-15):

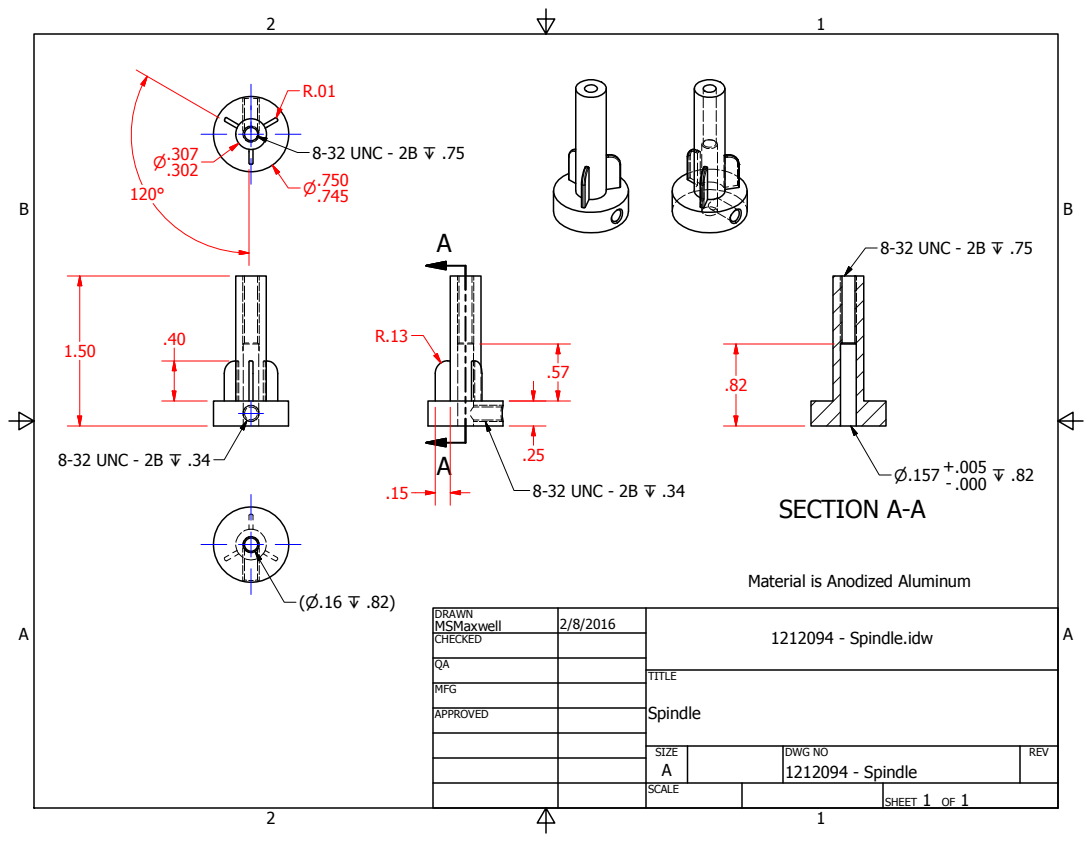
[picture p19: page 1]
SECTION A-A; DRAWN MSMaxwell CHECKED; MFG; APPROVED; 1212094 - Spindle.idw; TITLE; Spindle; SIZE A; SCALE; DWG NO 1212094 - Spindle; REV; SHEET 1 OF 1; 8-32 UNC - 2B Z .75; 8-32 UNC - 2B Z .34

Material is Anodized Aluminum

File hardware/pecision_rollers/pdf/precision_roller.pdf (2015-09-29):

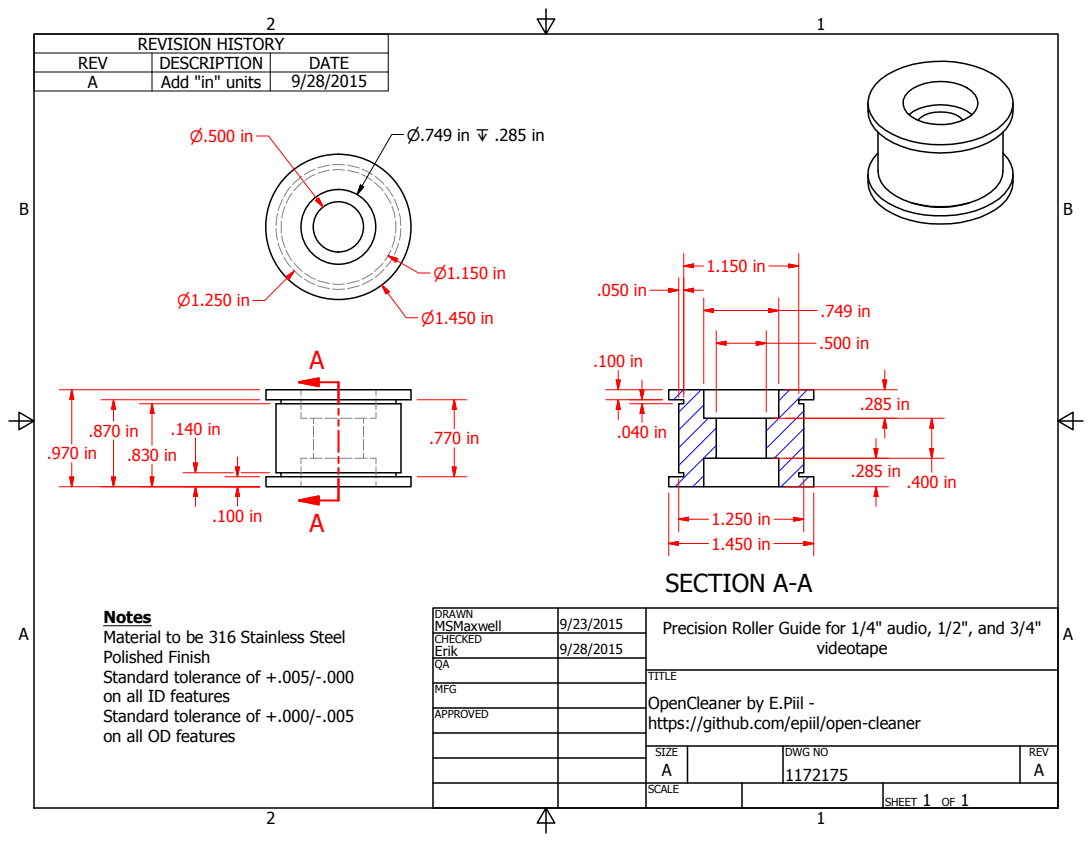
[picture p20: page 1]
SECTION A-A; DRAWN MSMaxwell CHECKED Erik QA; MFG; APPROVED; videotape; SIZE A; SCALE; DWG NO 1172175; REV A; SHEET 1 OF 1; REVISION HISTORY; REV; DESCRIPTION; DATE; Add "in" units

Notes
Material to be 316 Stainless Steel
Polished Finish
Standard tolerance of +.005/-.000
on all ID features
Standard tolerance of +.000/-.005
on all OD features

Precision Roller Guide for 1/4" audio, 1/2", and 3/4"

TITLE
OpenCleaner by E.Piil -
https://github.com/epiil/open-cleaner

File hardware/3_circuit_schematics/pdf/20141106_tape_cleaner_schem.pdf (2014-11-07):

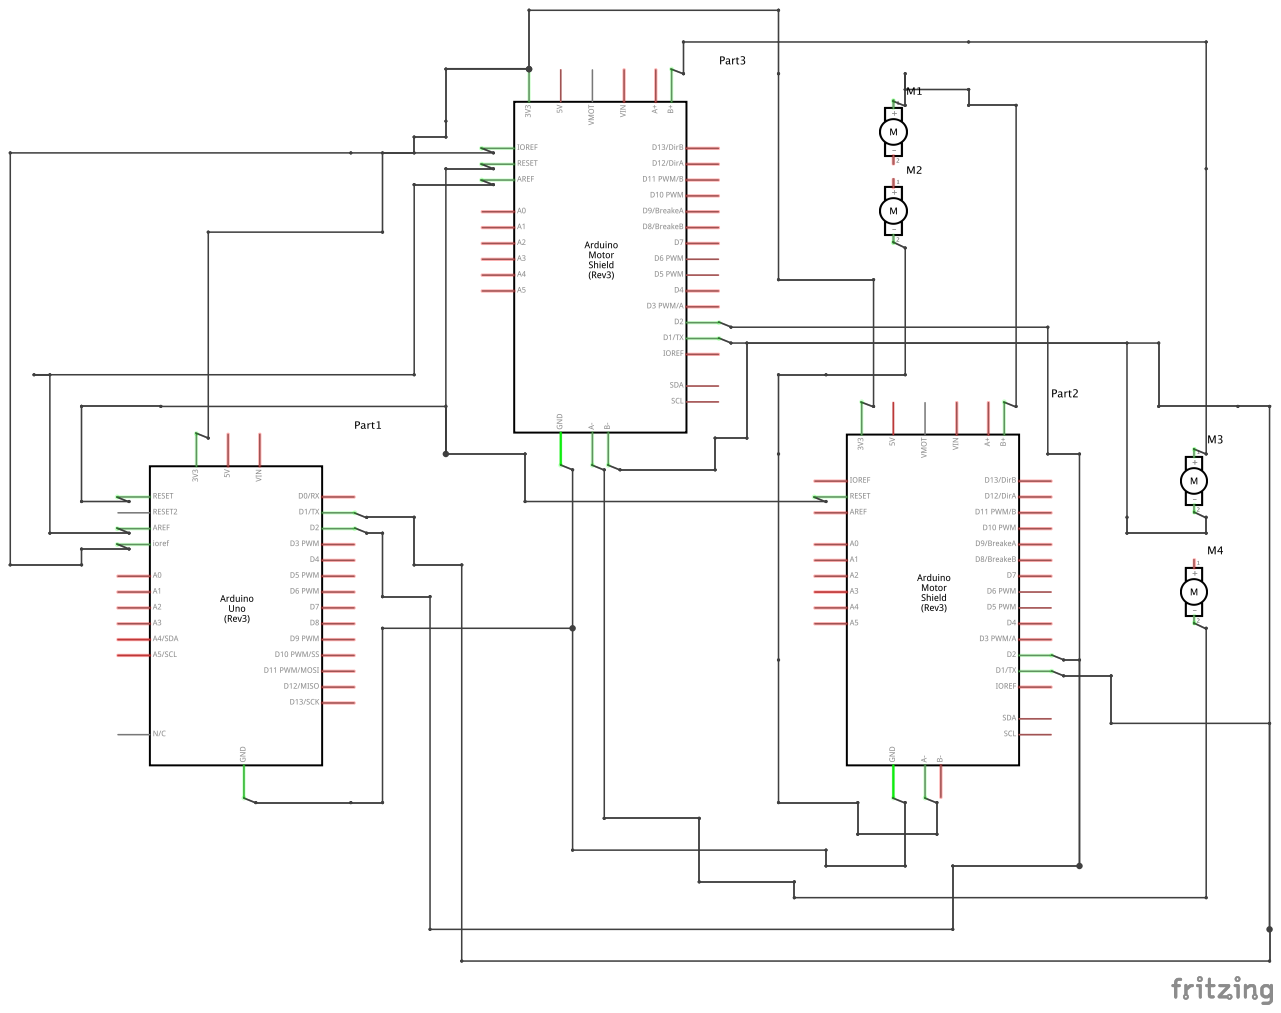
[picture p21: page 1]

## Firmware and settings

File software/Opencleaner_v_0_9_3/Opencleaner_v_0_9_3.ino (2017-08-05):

/* 
Opencleaner v.0.9.3
5 August 2017
https://github.com/epiil/open-cleaner
*/
// ============================================================================================
//        ARDUINO LIBRARIES
//=============================================================================================

#include <Wire.h> // Library for communicating with I2C devices
#include <Adafruit_MotorShield.h> // Library for Adafruit Motor Shield
#include <Adafruit_MCP23017.h> // Library for MCP23017 I2c Port Expander
#include <Adafruit_RGBLCDShield.h> // Adafruit RGB LCD Shield Library
#include <SimpleTimer.h> // SimpleTimer Library for measuring RPM
#include <digitalWriteFast.h> //digitalWriteFast Library
#include <PID_v1.h> // PID Library
#include <EEPROMex.h> // Library for writing to EEPROM
#include <EEPROMVar.h> // Library for writing to EEPROM

// ============================================================================================
//        ADAFRUIT MOTOR SHIELD v.2 - for PELLON MOTORS
//=============================================================================================

Adafruit_MotorShield AFMS = Adafruit_MotorShield(0X61); // Creates motor shield object with alternate 0x61 I2C address
Adafruit_DCMotor *pellonMotor1 = AFMS.getMotor(1); // assigns Supply-side Pellon motor to M3 on the Adafruit Motor Shield
Adafruit_DCMotor *pellonMotor2 = AFMS.getMotor(2); // assigns Takeup-side Pellon motor to M4 on the Adafruit Motor Shield

// Variables

int pellonMotorSpeed = 100; // Initial pellon motor speed (100/255)

// ============================================================================================
//        CYTRON MDD10A DC MOTOR DRIVER - for SPINDLE MOTORS
//=============================================================================================

const int takeupinterruptPin = 2;

#define spindlesupplyMotor_DIR1 8   // Assigns DIR1 on MDD10A to Digital Pin 8    11
#define spindlesupplyMotor_PWM1 9   // Assigns PWM1 on MDD10A to Digital Pin 9  (PWM pin) 10
#define spindletakeupMotor_PWM2 10  // Assigns PWM2 on MDD10A to Digital Pin 10 (PWM pin) 9
#define spindletakeupMotor_DIR2 11  // Assigns DIR2 on MDD10A to Digital Pin 11 8

// Variables

int supplyMotorSpeed = 10; // Initial supply spindle motor speed (100/255)
int spindlesupplyMotor_PWM = 10; // PWM value for supply spindle motor

int takeupMotorSpeed = 10; // Initial takeup spindle motor speed (100/255)
int spindletakeupMotor_PWM = 10; // PWM value for takeup spindle motor
//takeupMotorSpeed = constrain(takeupMotorSpeed, 0, 255); //limits takeupMotorSpeed value 0-255

int spindlesupplyMotor_DIR = 0;
int spindletakeupMotor_DIR = 0; 

boolean spindlesupplyMotor_RUN_FLAG = false;
boolean spindletakeupMotor_RUN_FLAG = false;

int spindletakeupMotorSpeed = 0; //REMOVE??
int spindlesupplyMotorSpeed = 0;


// ============================================================================================
//        PITTMAN E30 INCREMENTAL OPTICAL ENCODERS - 512 counts per resolution (CPR)
//=============================================================================================

#define spindletakeupOpticalEncoderPinB 2 // Assigns Supply Spindle Motor Optical Encoder Channel A to Arduino Digital Pin 2
#define spindletakeupOpticalEncoderIsReversed

// Variables

volatile bool spindlesupplyOpticalEncoderASet;
volatile long spindlesupplyOpticalEncoderCount = 0;

volatile bool spindletakeupOpticalEncoderBSet;
volatile long spindletakeupOpticalEncoderCount = 0;

unsigned int spindlesupplymotorSpeedRPM=0;                      //    Calculated motor speed from encoder value.
unsigned int spindletakeupmotorSpeedRPM=0;

SimpleTimer timer;                                             //     Timer object for polling counter value every 1 sec.

const long updateInterval=1000L;                              //      Timer update value (1000 ms)
const float pulsesPerRevolution=256*2.0;                     //       Pulses per revolution (512 CPR)


// ============================================================================================
//        OPTEK OPB819Z SLOTTED OPTICAL SWITCH for TAPESENSORREAD 
//=============================================================================================

int optotapeSensor = 5; //Assigns Opto Switch (tape sensor) collector to Arduino Digital Pin 5

// ============================================================================================
//        BOURNS EM14 ROTARY OPTICAL ENCODER (aka TENSION ENCODER) - 64 pulses per revolution (PPM)
//=============================================================================================

int val; 
int tensionencoderChannelA = 6;          // Stores rotary optical encoder Channel A as Pin 6
int tensionencoderChannelB = 7;          // Stores rotary optical encoder Channel B as Pin 7
int tensionencoder0Pos = 0;           // Rotary optical encoder position at 0
int tensionencoderChannelALast = LOW;
int n = LOW;

// ============================================================================================
//        ADAFRUIT RGB LCD KEYPAD 
//=============================================================================================

#define LED 13 // Adafruit RGB LCD keypad
Adafruit_RGBLCDShield lcd = Adafruit_RGBLCDShield(); // LCD shield instantiation, creates LCD shield object
#define WHITE 0x7 // Sets background color (for RGB keypads)
#define BUTTON_SHIFT BUTTON_SELECT 

// Variables
unsigned long lastInput = 0; // last button press
const int logInterval = 10000; // log every 10 seconds
long lastLogTime = 0;

// ============================================================================================
//        OPERATING STATES
//=============================================================================================

enum operatingState { OPER = 0, RUNF, CLOSEDLOOP, PELRUN, MENUSUPPLYSPEED, MENUTAKEUPSPEED, TUNE_P, TUNE_I, TUNE_D, OPTOREAD, TENSIONREAD, TAPESENSORREAD};
operatingState opState = OPER;

boolean TAPE_SPEED_OPTO_STATE = false;
boolean LAST_TAPE_SPEED_OPTO_STATE = false;         // Used for debouncing

float spindletakeupMotorSpeed_FLOAT = 0.0;
float spindlesupplyMotorSpeed_FLOAT = 0.0;

// ============================================================================================
//        PID VARIABLES AND CONSTANTS
//=============================================================================================

double Setpoint, Input, Output;
double spindlesupplyMotor_PID_Kp = 1;
double spindlesupplyMotor_PID_Ki = 0.1;
double spindlesupplyMotor_PID_Kd = 0.05;

PID myPID(&Input, &Output, &Setpoint, spindlesupplyMotor_PID_Kp, spindlesupplyMotor_PID_Ki, spindlesupplyMotor_PID_Kd, DIRECT);

// ============================================================================================
//        FUNCTION: UPDATE SPEED EVENT
//=============================================================================================

/*void updatesupplySpeedEvent()
{
  spindlesupplymotorSpeedRPM=((spindlesupplyOpticalEncoderCount/(updateInterval/1000.0))*60.0)/pulsesPerRevolution; //RPM speed
  spindlesupplyOpticalEncoderCount=0; //reset counter;
  
} // =========== End updateSpeedEvent Function =============*/

// ============================================================================================
//        FUNCTION: UPDATE TAKEUP SPEED EVENT
//=============================================================================================

void updateSpeedEvent()
{
  spindletakeupmotorSpeedRPM=((spindletakeupOpticalEncoderCount/(updateInterval/1000.0))*60.0)/pulsesPerRevolution; //RPM speed
  spindletakeupOpticalEncoderCount=0; //reset counter;
  
} // =========== End updateSpeedEvent Function =============

// ============================================================================================
//        FUNCTION: MC3886 MOTOR DRIVER - SPEED
//=============================================================================================

void spindlesupplyMotor_SET_SPEED(int SPEED)
{
  spindlesupplyMotor_PWM = SPEED;
  if(spindlesupplyMotor_RUN_FLAG)
  switch (spindlesupplyMotor_DIR)
  {
    case BACKWARD:
      spindlesupplyMotor_RUN_FLAG = true;
      digitalWrite(spindlesupplyMotor_DIR1,LOW); // writes 0/1023 duty to spindletakeupMotor_PWM1 pwm pin
      analogWrite(spindlesupplyMotor_PWM1,SPEED); // Configures spindletakeupMotor_PWM12 pwm pin, duty SPEED
    break;
  }
} // =========== End MC3886 Motor Driver Supply Set Speed Function =============

void spindletakeupMotor_SET_SPEED(int SPEED)
{
  spindletakeupMotor_PWM = SPEED;
  if(spindletakeupMotor_RUN_FLAG)
  switch (spindletakeupMotor_DIR)
  {
    case FORWARD:
      spindletakeupMotor_RUN_FLAG = true;
      digitalWrite(spindletakeupMotor_DIR2,HIGH); // writes 1023/1023 duty to spindletakeupMotor_DIR2 pin
      analogWrite(spindletakeupMotor_PWM2,SPEED); // Configures spindletakeupMotor_PWM1 pwm pin, duty SPEED
    break;
  }
} // =========== End MC3886 Motor Driver Takeup Set Speed Function =============

// ============================================================================================
//        FUNCTION: MC3886 MOTOR DRIVER - DIRECTION
//=============================================================================================

void spindletakeupMotor_RUN(int DIRECTION)
{
  spindletakeupMotor_DIR = DIRECTION;
  switch (DIRECTION)
  {
    case FORWARD:
      spindletakeupMotor_RUN_FLAG = true; 
      digitalWrite(spindletakeupMotor_DIR2,HIGH);
      analogWrite(spindletakeupMotor_PWM2, spindletakeupMotor_PWM);
    break;
    case BRAKE:
      spindletakeupMotor_RUN_FLAG = false;
      digitalWrite(spindletakeupMotor_PWM2,LOW);
      digitalWrite(spindletakeupMotor_DIR2, LOW);
    break;
    case RELEASE: 
      spindletakeupMotor_RUN_FLAG = false;
      digitalWrite(spindletakeupMotor_PWM2,LOW);
      digitalWrite(spindletakeupMotor_DIR2, LOW);
    break;
  }
} // =========== End MC3886 Motor Driver Takeup Direction Function =============

void spindlesupplyMotor_RUN(int DIRECTION)
{
  spindlesupplyMotor_DIR = DIRECTION;
  switch (DIRECTION)
  {
    case BACKWARD:
      spindlesupplyMotor_RUN_FLAG = true;
      digitalWrite(spindlesupplyMotor_DIR1,LOW);
      analogWrite(spindlesupplyMotor_PWM1, spindlesupplyMotor_PWM); 
    break;
    case BRAKE:
      spindlesupplyMotor_RUN_FLAG = false;
      digitalWrite(spindlesupplyMotor_PWM1,LOW);
      digitalWrite(spindlesupplyMotor_DIR1,LOW);
    break;
    case RELEASE: 
      spindlesupplyMotor_RUN_FLAG = false;
      digitalWrite(spindlesupplyMotor_PWM1,LOW);
      digitalWrite(spindlesupplyMotor_DIR1,LOW);
    break;
  }
} // // =========== End MC3886 Motor Driver Supply Direction Function =============

// ============================================================================================
//        MAIN SETUP FUNCTION
//=============================================================================================

void setup() {
  
  Serial.begin (9600); // Begin serial 

  pinMode(spindletakeupOpticalEncoderPinB, INPUT);                    // sets pin A as input
  digitalWrite(spindletakeupOpticalEncoderPinB, LOW);                 // turn on pullup resistors
  attachInterrupt(digitalPinToInterrupt(takeupinterruptPin), spindletakeupOpticalEncoderInterruptB, RISING);

  /*pinMode(spindlesupplyOpticalEncoderPinA, INPUT);                    // sets pin A as input
  digitalWrite(spindlesupplyOpticalEncoderPinA, LOW);                 // turn on pullup resistors
  attachInterrupt(digitalPinToInterrupt(supplyinterruptPin), spindlesupplyOpticalEncoderInterruptA, RISING);*/
  
  timer.setInterval(updateInterval, updateSpeedEvent);                // Interrupt for accurate counting of encoder pulses
  //timer.setInterval(updateInterval, updatesupplySpeedEvent);               
  
   lcd.begin(16, 2);
   lcd.print(F("Opencleaner v0.9")); // Opening Display with version control
   delay(900);

   pinMode(LED,OUTPUT); // Configures LED pin as output
   pinMode(spindlesupplyMotor_PWM1,OUTPUT); // Configures supply motor pin as output
   pinMode(spindlesupplyMotor_DIR1,OUTPUT); // Configures supply motor pin as output
   pinMode(spindletakeupMotor_PWM2,OUTPUT); // Configures takeup motor pin as output
   pinMode(spindletakeupMotor_DIR2,OUTPUT); // Configures takeup motor pin as output

   pinMode(tensionencoderChannelA,INPUT); // Configures tension rotary encoder channel A as input
   pinMode(tensionencoderChannelB,INPUT); // Configures tension rotary encoder channel B as input

   AFMS.begin();  // Sets default frequency at 1.6KHz
   TCCR1B = (TCCR1B & 0b11111000) | 1;  // Adjust PWM frequency of PWM Pins 9 & 10 to 31372.55 Hz (31 kHz), removes audible PWM squeel

   pellonMotorSpeed = 100; // Intial spindle motor speed at 100/255
   pellonMotor1->setSpeed(pellonMotorSpeed); // Sets initial Supply motor to 100/255
   pellonMotor2->setSpeed(pellonMotorSpeed); // Sets initial Takeup motor to 100/255
   pellonMotor1->run(RELEASE); // Turns pellon 1 motor off
   pellonMotor2->run(RELEASE); // Turns pellon 2 motor off

// PID

   Input = spindletakeupmotorSpeedRPM;
   Setpoint = 50; // 170/255=39% power / rpm for dc motor
   myPID.SetMode(AUTOMATIC);
   myPID.SetOutputLimits(20, (int) 220);

// Read Parameters from EEPROM

   #define spindlesupplyMotor_PID_Kp_EEPROM_ADDRESS 0
   #define spindlesupplyMotor_PID_Ki_EEPROM_ADDRESS 4
   #define spindlesupplyMotor_PID_Kd_EEPROM_ADDRESS 8

   EEPROM.writeDouble(spindlesupplyMotor_PID_Kp_EEPROM_ADDRESS,0.5);
   EEPROM.writeDouble(spindlesupplyMotor_PID_Ki_EEPROM_ADDRESS,0.1);
   EEPROM.writeDouble(spindlesupplyMotor_PID_Kd_EEPROM_ADDRESS,0.1);

   spindlesupplyMotor_PID_Kp = EEPROM.readDouble(spindlesupplyMotor_PID_Kp_EEPROM_ADDRESS);
   spindlesupplyMotor_PID_Ki = EEPROM.readDouble(spindlesupplyMotor_PID_Ki_EEPROM_ADDRESS);
   spindlesupplyMotor_PID_Kd = EEPROM.readDouble(spindlesupplyMotor_PID_Kd_EEPROM_ADDRESS);

} // =========== End Setup Function =============

// ============================================================================================
//        MAIN LOOP FUNCTION
//=============================================================================================

void loop() { 
  while(ReadButtons() != 0) {}
  lcd.clear();
  switch (opState) {
    case OPER:
    Oper();
    break;
    case RUNF: // Menu: Run tape forward
    RunF();
    break;
    case CLOSEDLOOP: // Menu: Run Closed Loop
    ClosedLoop();
    break;
    case PELRUN: // Menu: Run Pellon Motors Forward, Set Pellon Motor Speed
    PelRun();
    break;
    case MENUSUPPLYSPEED: // Menu: Set Supply Spindle Speed
    MenuSupplySpeed();
    break;
    case MENUTAKEUPSPEED: // Menu: Set Menu Takeup Speed
    MenuTakeUpSpeed();
    break;
    case TUNE_P: // Menu: Tune Proportional settings of PID loop
    TuneP();
    break;
    case TUNE_I: // Menu: Tune Integral settings of PID loop
    TuneI();
    break;
    case TUNE_D: // Menu: Tune Damping/Derivative settings of PID loop
    TuneD();
    break;
    case OPTOREAD: // Menu: Read tape speed optical encoder
    OptoRead();
    break;
    case TENSIONREAD: // Menu: Read tension encoder
    TensionRead();
    break;
    case TAPESENSORREAD: // Menu: Read tape tension opto switch
    TapeSensorRead();
    break;
    timer.run(); // Initiates SimpleTimer
   }
} // =========== End Loop Function =============

// ============================================================================================
//        READBUTTONS - All keypad buttons are read at once, returns a variable that has individual bits set for the buttons
//=============================================================================================
uint8_t ReadButtons()
{
  uint8_t buttons = lcd.readButtons();
  if (buttons != 0)
  {
    lastInput = millis();
  }
  return buttons;
} // =========== End ReadButtons Function =============

// ===============================================
// OFF STATUS
// RIGHT - LOAD
// LEFT - TENSIONREAD
// ===============================================
void Oper()
{
  lcd.print(F("1.Operations:"));
  lcd.setCursor(0, 1);
  lcd.print(F("< Back    Menu >"));
  uint8_t buttons = 0;
  while(true)
  {
      buttons = ReadButtons();
      if (buttons & BUTTON_SHIFT)
      {
      }
      if (buttons & BUTTON_LEFT)
      {
         opState = TAPESENSORREAD;
         return;
      }
      if (buttons & BUTTON_RIGHT)
      {
         opState = RUNF;
         return;
      }
  }
} // =========== End Oper Function =============

// ===============================================
// Run Forward
// RIGHT button: for PELRUN
// LEFT button: for OPER
// SHIFT button: 
// ===============================================
void RunF()
{
  lcd.print(F("2.Clean Forward"));
  lcd.setCursor(0,1);
  lcd.print(F("UP to RUN"));
  uint8_t buttons = 0;
  while(true)
  {
      buttons = ReadButtons();
      
      if (buttons & BUTTON_SHIFT)
      {
        spindlesupplyMotor_RUN(BRAKE);
        spindletakeupMotor_RUN(BRAKE);
        pellonMotor1->run(RELEASE);
        pellonMotor2->run(RELEASE);
        lcd.setCursor(13,1);
        lcd.print(F("STP"));
      }
      if (buttons & BUTTON_LEFT)
      {
         opState = OPER;
         return;
      }
      if (buttons & BUTTON_RIGHT)
      {
         opState = PELRUN;
         return;
      }
      if (buttons & BUTTON_UP)
      {
        opState = CLOSEDLOOP;
         return;
      }
      if (buttons & BUTTON_DOWN)
      {
      }
      if  (digitalRead(optotapeSensor) == 0)  //Opto switch beam is seen
      {
        spindlesupplyMotor_RUN(BRAKE);
        spindletakeupMotor_RUN(BRAKE);
        pellonMotor1->run(RELEASE);
        pellonMotor2->run(RELEASE);
      }
      else
      {
      }
  }
} // =========== End RunB Function =============

// ===============================================
// BACKWARDS CLOSED LOOP STATUS aka CLOSEDLOOP
// SHIFT and RIGHT for autotune
// RIGHT - Setpoint
// LEFT - TENSIONREAD
// ===============================================
void ClosedLoop()
{
  lcd.print(F("2.Clean(Reverse)"));
  lcd.setCursor(0,1);
  lcd.print(F("RPM:"));
  uint8_t buttons = 0;
  while(true)
  {
      buttons = ReadButtons();
      if (buttons & BUTTON_SHIFT)
      {
        spindlesupplyMotor_RUN(BRAKE);
        spindletakeupMotor_RUN(BRAKE);
        pellonMotor1->run(RELEASE); // Turns pellon 1 motor off
        pellonMotor2->run(RELEASE); // Turns pellon 2 motor off
      }
      if (buttons & BUTTON_LEFT)
      {
         opState = RUNF;
         return;
      }
      if (buttons & BUTTON_RIGHT)
      {
         opState = PELRUN;
         return;
      }
      readtapetension();
      reversetensionClosedLoop();
      analogWrite(spindlesupplyMotor_PWM1, 10);
      timer.run(); // Initiates SimpleTimer
      Serial.print("supply motor speed (RPM) = ");
      Serial.print(spindletakeupmotorSpeedRPM);
      Serial.print(" Output = ");
      Serial.print(Output);   
      Serial.print(" Tape Tension = ");
      Serial.print(tensionencoder0Pos);   
      Serial.print("\n");
      lcd.setCursor(5,1);
      lcd.print(spindletakeupmotorSpeedRPM);
      lcd.print("    ");
      if  (digitalRead(optotapeSensor) == 0)  //Opto switch beam is seen
      {
        spindlesupplyMotor_RUN(BRAKE);
        spindletakeupMotor_RUN(BRAKE);
        pellonMotor1->run(RELEASE); // Turns pellon 1 motor off
        pellonMotor2->run(RELEASE); // Turns pellon 2 motor off
      }
      else
      {
        pellonMotor1->run(FORWARD);
        pellonMotor2->run(FORWARD);
        runClosedLoop();
      } 
      delay(20);
      
  }
} // =========== End ClosedLoop Function =============

// ===============================================
// MENU: Run Pellon aka PELRUN
// RIGHT button: for MENUSUPPLYSPEED
// LEFT button: for RUNB
// SHIFT button: - Run Pellon
// ===============================================
void PelRun()
{
  lcd.print(F("3.Pellon"));
  lcd.setCursor(12,0);
  lcd.print(F("/255"));
  uint8_t buttons = 0;
  while(true)
  {
      buttons = ReadButtons();
      float increment = 5.0;
      if (buttons & BUTTON_SHIFT)
      {
      pellonMotor1->run(RELEASE);
      pellonMotor2->run(RELEASE);
      lcd.setCursor(13,1);
      lcd.print(F("STP"));
      }
      if (buttons & BUTTON_LEFT)
      {
         opState = RUNF;
         return;
      }
      if (buttons & BUTTON_RIGHT)
      {
         opState = MENUSUPPLYSPEED;
         return;
      }
      if (buttons & BUTTON_UP)
      {
        pellonMotorSpeed += increment;
        delay(200);
        pellonMotor1->setSpeed(pellonMotorSpeed);
        pellonMotor2->setSpeed(pellonMotorSpeed);
        pellonMotor1->run(FORWARD);
        pellonMotor2->run(FORWARD);
        lcd.setCursor(9,0);
        lcd.print("   ");
        lcd.setCursor(9,0);
        lcd.print(pellonMotorSpeed);
      }
      if (buttons & BUTTON_DOWN)
      {
        pellonMotorSpeed -= increment;
        delay(200);
        pellonMotor1->setSpeed(pellonMotorSpeed);
        pellonMotor2->setSpeed(pellonMotorSpeed);
        pellonMotor1->run(FORWARD);
        pellonMotor2->run(FORWARD);
        lcd.setCursor(9,0);
        lcd.print("   ");
        lcd.setCursor(9,0);
        lcd.print(pellonMotorSpeed);
      }
  }
} // =========== End PelRun Function =============
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

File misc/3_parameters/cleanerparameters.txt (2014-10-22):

Parameters:

-Capstan-less dual-motor spindle drivetrain

-Leader sensing system 

-Automatically stop and reverse when tape is nearing end

-Tape speed and tension monitoring (approximately 120 ips on average). Tension sensor arm measures tape tension.

-Two cleaning stations at center with automatic advance, forward, rewind

-Adjustable spindle flanges based on format

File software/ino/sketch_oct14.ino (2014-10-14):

#include <Servo.h> 
 
Servo pellonservo1;  // create pellonservo1 object 
Servo pellonservo2;  // create pellonservo2 object
                
int pos = 0;    // variable to store servo position 

#include <AFMotor.h>

AF_DCMotor motorsupply(1);
AF_DCMotor motortakeup(2);
 
void setup() 
{ 
  pellonservo1.attach(9);  // attaches the servo on pin 9 to the servo object 
  pellonservo2.attach(10);  // attaches the servo on pin 9 to the servo object
  for(pos = 0; pos < 1; pos += 1)  // goes from 0 degrees to 1 degrees 
  {                                  // in steps of 1 degree 
    pellonservo1.write(pos);              // tell servo to go to position in variable 'pos'
    pellonservo2.write(pos);              // tell servo to go to position in variable 'pos' 
    delay(100);                       // waits 15ms for the servo to reach the position 
  } 
   Serial.begin(9600);           // set up Serial library at 9600 bps
  Serial.println("Motor 1, 2, 3, 4 test");
    motorsupply.setSpeed(1000);
    motortakeup.setSpeed(1000);
  motorsupply.run(RELEASE);
  motortakeup.run(RELEASE);
}

int i;

void loop() {
  motorsupply.run(FORWARD);
  motortakeup.run(FORWARD);
  for (i=0; i<255; i++) {
    motorsupply.setSpeed(i); 
    motortakeup.setSpeed(i); 
    delay(70);
 }
 
  for (i=255; i!=0; i--) {
    motorsupply.setSpeed(i);
    motortakeup.setSpeed(i);  
    delay(70);
 }
 
  motorsupply.run(BACKWARD);
  motortakeup.run(BACKWARD);
  for (i=0; i<255; i++) {
    motorsupply.setSpeed(i); 
    motor2.setSpeed(i); 
    delay(70);
 }
 
  for (i=255; i!=0; i--) {
    motorsupply.setSpeed(i); 
    motortakeup.setSpeed(i); 
    delay(70);
 }
}

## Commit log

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2014-10-22 Added OpenSCAD spindle layouts
    UMatic and 1/4” and 1/2” formats
    [QuarterInchHalfInchSpindle.scad, UMatic_spindle.scad]
2014-10-22 Added spindle STLs (work in progress)
    [QuarterInchHalfInchSpindle.scad, UMatic_spindle.scad, UMatic_spindle.stl]
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2014-10-23 added SketchUp working files
    [TapeCleaner.dxf, TapeCleaner.skp]
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2014-10-23 added detail to sketch
    [TapeCleaner.skp]
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2014-11-05 cleaner sketch in tinkercad
    [tape_cleaner.stl]
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2014-11-10 Cleaned up file naming, added legacy folder
    [20131023_TapeCleaner.skp, 20131023_TapeCleaner~.skp, 20141022_QuarterInchHalfInchSpindle.scad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]
2014-11-13 added motor shield schematics
    [Shield_Motor-REV3c.brd, Shield_Motor-REV3c.sch]
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2014-11-16 added DPDT and SPDT switches
    [20141116_tape_cleaner.fzz]
2014-11-16 cleaned up file naming
    [20141106_tape_cleaner.fzz]
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2015-03-10 start enclosure top cutouts
    [20150310_DesktopEnclosureTopCutouts.scad]
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2015-03-11 2D scad and dxf
    [20150310_DesktopEnclosureTopCutouts2D.scad, Enclosuretop2D.dxf]
2015-03-11 2D and 3D enclosure top
    [20150310_DesktopEnclosureTopCutouts2D.scad, EnclosureTop3D.stl, Enclosuretop2D.dxf]
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2015-03-11 scads and stls with combined parts
    [DesktopEnclosureWithParts.scad, DesktopEnclosureWithParts.stl]
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2015-03-12 updated scad and stl
    [DesktopEnclosureWithParts.scad, DesktopEnclosureWithParts.stl]
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2015-03-12 updated enclosure scad, stl, 2d and 3d
    [20150310_DesktopEnclosureTopCutouts2D.scad, 20150310_DesktopEnclosureTopCutouts3D.scad]
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2015-03-13 update scads and dxf
    [20150310_DesktopEnclosureTopCutouts3D.scad, DesktopEnclosureTopCutouts.dxf, DesktopEnclosureTopCutouts.scad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]
2015-03-13 added photoops and IR sensors
    [DesktopEnclosureTopCutouts2D.dxf, DesktopEnclosureWithParts.scad, DesktopEnslocureWithParts.stl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]
2015-03-13 individual scads for objects
    [GuideRollerScres.scad, GuideRollers.scad, IRSensors.scad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]
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2015-03-14 updated STL and SCAD
    [DesktopEnclosureWithParts.scad, DesktopEnclosureWithParts.stl]
2015-03-15 updated STL and SCAD - revised roller guides
    [20150310_DesktopEnclosureTopCutouts2D.scad, DesktopEnclosureWithParts.scad, DesktopEnclosureWithParts.stl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]
2015-03-15 STL and SCAD - motor spindle
    [MotorSpindle.scad, MotorSpindle.stl]
2015-03-15 2D finalized DXF for front and back panels
    [BackPanel2D.dxf, BackPanel2D.scad, DesktopEnclosureWithParts.scad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]
2015-03-16 deleted old STL, cleaned up filenaming convention
    [20150310_DesktopEnclosure.scad, 20150310_DesktopEnclosureTopCutouts3D.scad, BackPanel.dxf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]
2015-03-16 updated SCAD, STL, DXF - adjustable guide slots
    [TapeCleaner.scad, TapeCleaner.stl, TopPanel.dxf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]
2015-03-16 updated UMatic spindle STL and SCAD
    [20141022_QuarterInchHalfInchSpindle.scad, 20141104_Halfinch_spindle.stl, 20141104_UMatic_spindle copy 2.scad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]
2015-03-16 added wiggle-room in roller cutouts
    [TopPanel.dxf, TopPanel2D.scad]
2015-03-18 updated history, cleaned up files, etc.
    [20141115_tape_cleaner.fzz, 20141116_tape_cleaner.fzz, Shield_Motor-REV3c.brd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]
2015-03-19 adjusted top width to 15.36"
    [TapeCleaner.scad, TapeCleaner.stl, TopPanel.dxf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]
2015-03-19 cleaned up file naming and directory
    [Shield_Motor-REV3c.brd, Shield_Motor-REV3c.sch]
2015-03-21 revised Umatic spindle prongs
    [UMaticSpindle.scad, UmaticSpindle.stl]
2015-03-22 updated Umatic spindle high render quality
    [UMaticSpindle.scad, UmaticSpindle.stl]
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2015-04-04 updated fritz scheme, added pollen motors test sketch
    [tapecleaner.fzz]
2015-04-04 Moved schematics from Fritzing to Eagle
    [tapecleaner.brd, tapecleaner.fzz, tapecleaner.sch]
2015-04-05 removed .brd file, updated schematic
    [tapecleaner.brd, tapecleaner.sch]
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2015-04-05 updated main 3d scad sketch
    [TapeCleaner.scad, TapeCleaner.stl]
2015-05-23 updated parts list and tapecleaner SCAD
    [TapeCleaner.scad, TapeCleaner.stl]
2015-05-23 fixed interrupter typo
2015-05-27 added IR distance sensor holder
    [IRdistancesensorHolder.stl, IRDistanceSensorHolder.scad]
2015-05-27 ir distance sensor holder formatting
    [ir_distance_sensor_holder.scad, ir_distance_sensor_holder.stl]
2015-05-27 refined IR distance sensor holder
    [ir_distance_sensor_holder.scad, ir_distance_sensor_holder.stl]
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2015-05-28 work on 1/2" roller
    [tape_path_roller.scad, tape_path_roller.stl]
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2015-06-02 corrected measurements for rollers
    [tape_path_roller.scad, tape_path_roller.stl]
2015-06-02 2nd design for roller
    [UMaticSpindle.scad, tape_path_roller_2.scad, tape_path_roller_2.stl]
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2015-06-14 added parts price list CSV
    [OpenCleanerPartsList - Sheet1.csv]
2015-06-15 added LCD keypad holes - front panel
    [FrontPanel.dxf, FrontPanel2D.scad]
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2015-07-06 updated roller with corrected diameter
    [tape_path_roller.scad]
2015-07-06 updated parts list with roller spindle kits
    [OpenCleanerPartsList.csv]
2015-07-06 added bias to rollers
    [tape_path_roller.scad]
2015-07-06 removed depreciated roller sketch
    [tape_path_roller_2.scad, tape_path_roller_2.stl]
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2015-09-29 updated precision roller
    +fabrication drawing
    +stl
    +dwg
    +stp
    -scad
    [pecision_rollers.scad, precision_roller.dwg, precision_roller.stl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]
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
